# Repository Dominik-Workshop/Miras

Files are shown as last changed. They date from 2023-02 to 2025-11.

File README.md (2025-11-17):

# Miras

 


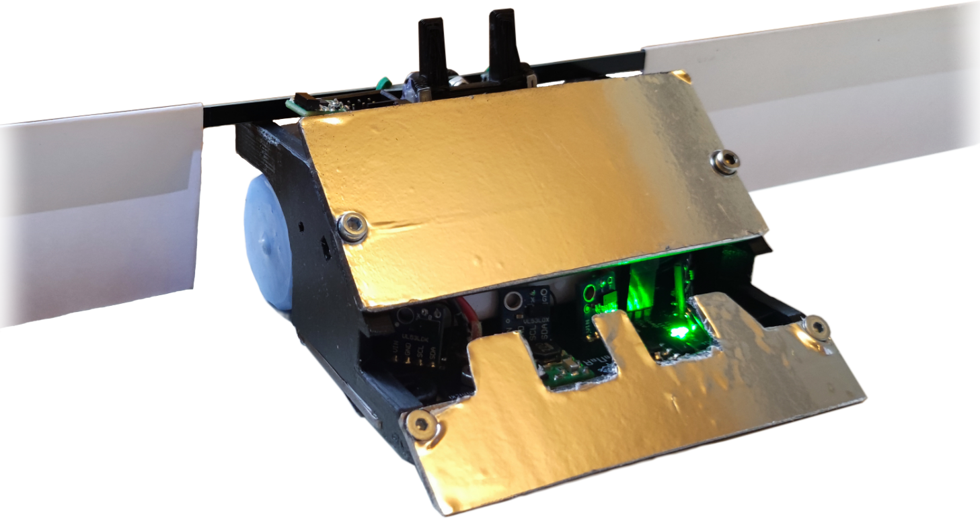
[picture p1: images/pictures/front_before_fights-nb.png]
Miras photo front


## Overview

Autonomous minisumo robot, based around an **STM32** microcontroller and **VL53L0X** TOF (time of flight) distance sensors, which provide necessary processing power and great detection range of opponents.

Its distinguishing feature is a set of **deployable wings**, designed to attract an opponent toward them, making them vulnerable to falling off the dohyo.

## Electronics

This project features two custom-designed PCBs that are connected via a flexible flat cable (FFC):

- [**Main board**](/pcb_main/): responsible for the robot's core functionalities. It integrates the microcontroller, sensors, motor drivers, and power management circuitry

<p align="center">
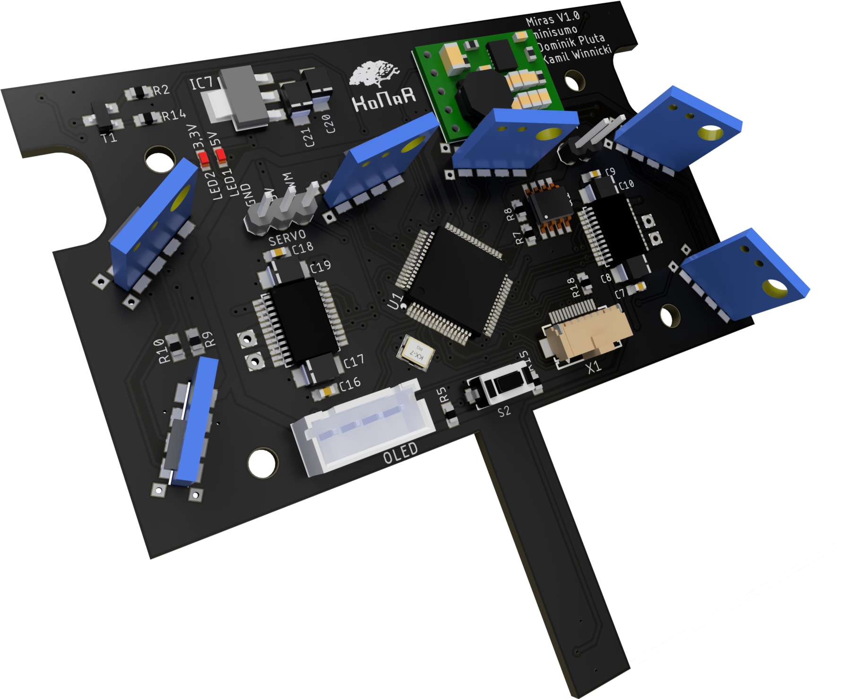
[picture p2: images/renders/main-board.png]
Main board render
  
</p>

- [**Top board**](/pcb_top/): accommodates an on/off switch, an SWD programming connector, configuration DIP switches, and a dedicated space for a standard [starter module](https://p1r.se/startmodule/)

<p align="center">
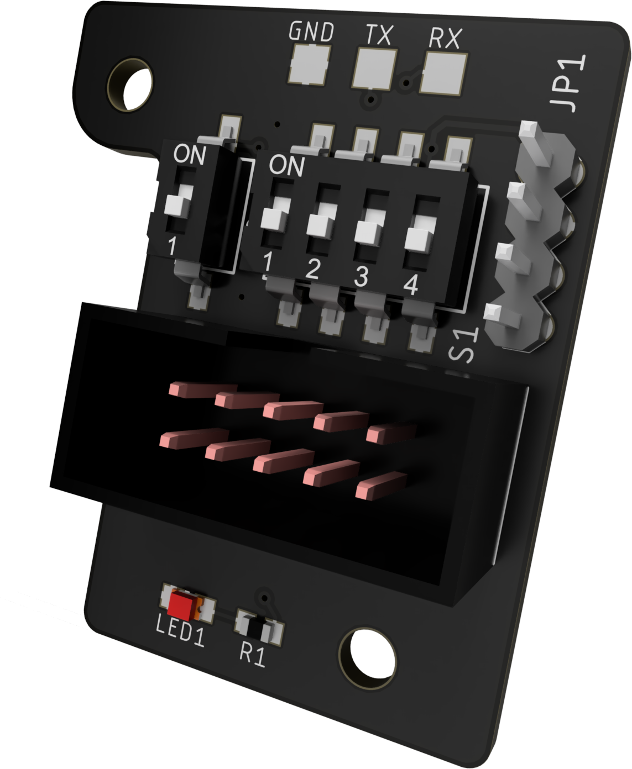
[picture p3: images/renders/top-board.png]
Top board render
   
</p>

The robot also features a 128x64px **OLED** screen for debugging.

<p align="center">
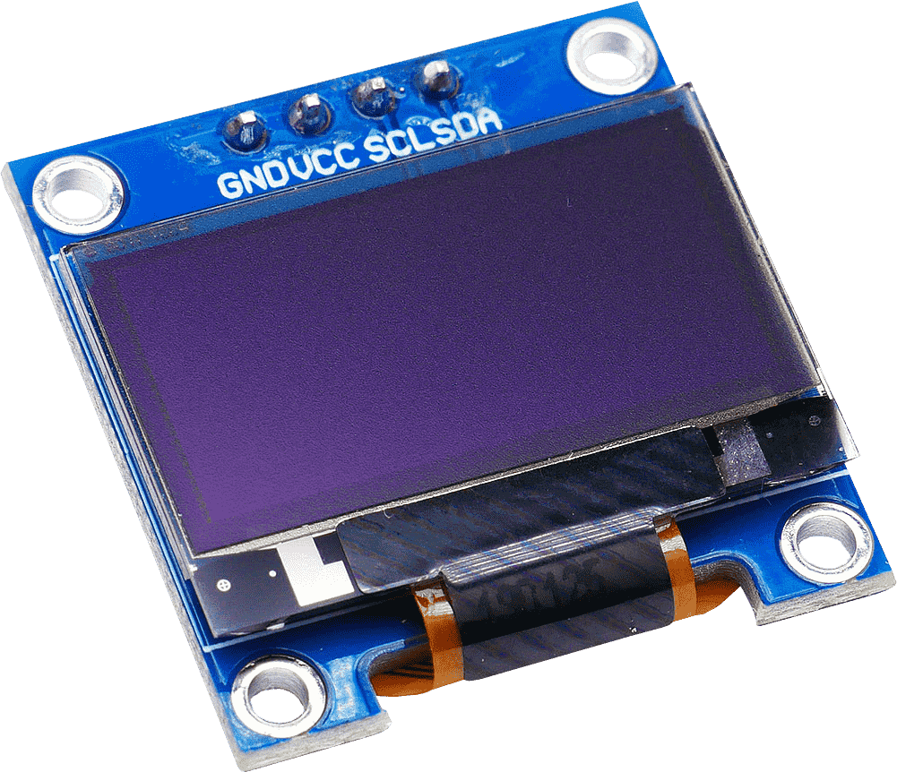
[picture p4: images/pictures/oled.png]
OLED photo
   
</p>

## Mechanical

<p align="center">
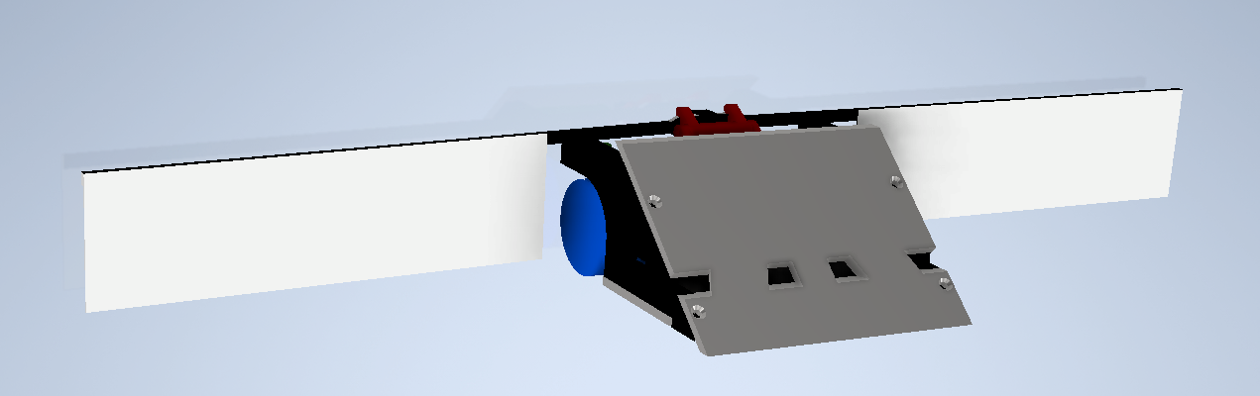
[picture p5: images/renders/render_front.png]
Miras render front
  
</p>

The chassis is a robust blend of 3D-printed components, steel, and aluminum, designed for durability and a low center of gravity. For superior traction on the dohyo, the robot is equipped with custom cast rubber tires. The unique deployable wings, made from lightweight paper, serve as the active deflection mechanism.

The robot is powered by two **N20** motors.

## Used Tools

- [Autodesk EAGLE](https://www.autodesk.com/products/eagle/) - Schematic and PCB design
- [Autodesk Inventor](https://www.autodesk.com/products/inventor/) - 3D modeling
- [STM32CubeIDE](https://www.st.com/en/development-tools/stm32cubeide.html) - STM32 firmware development (build/flash/debug)

## Authors

- [**Dominik Pluta**](https://github.com/Dominik-Workshop):
  - **Responsibility**: PCB design, programming
- [**Kamil Winnicki**](https://github.com/KamilWuu):
  - **Responsibility**: design and manufacturing of mechanical parts

## Special Thanks

Special thanks to [**Eryk Możdzeń**](https://github.com/Eryk-Mozdzen), who helped with programming.

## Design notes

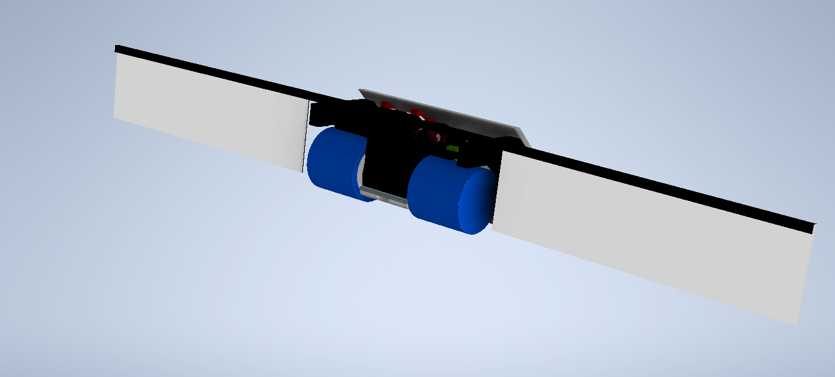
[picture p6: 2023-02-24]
images/renders/render_back.png

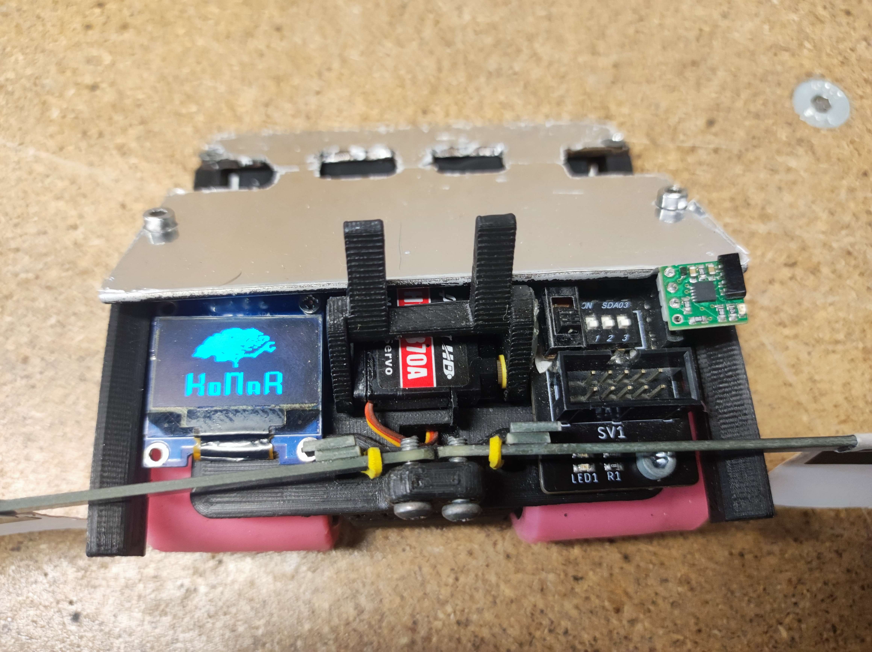
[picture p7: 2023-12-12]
images/pictures/top.jpg

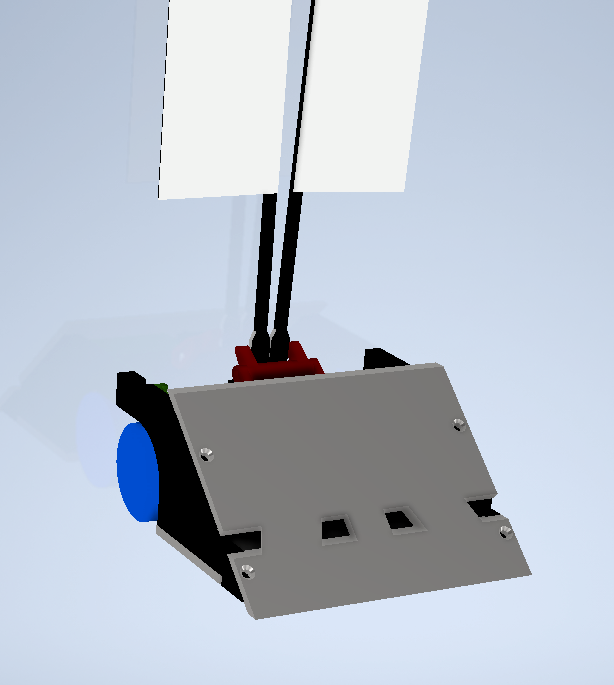
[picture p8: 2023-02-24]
images/renders/render_front_folded.png

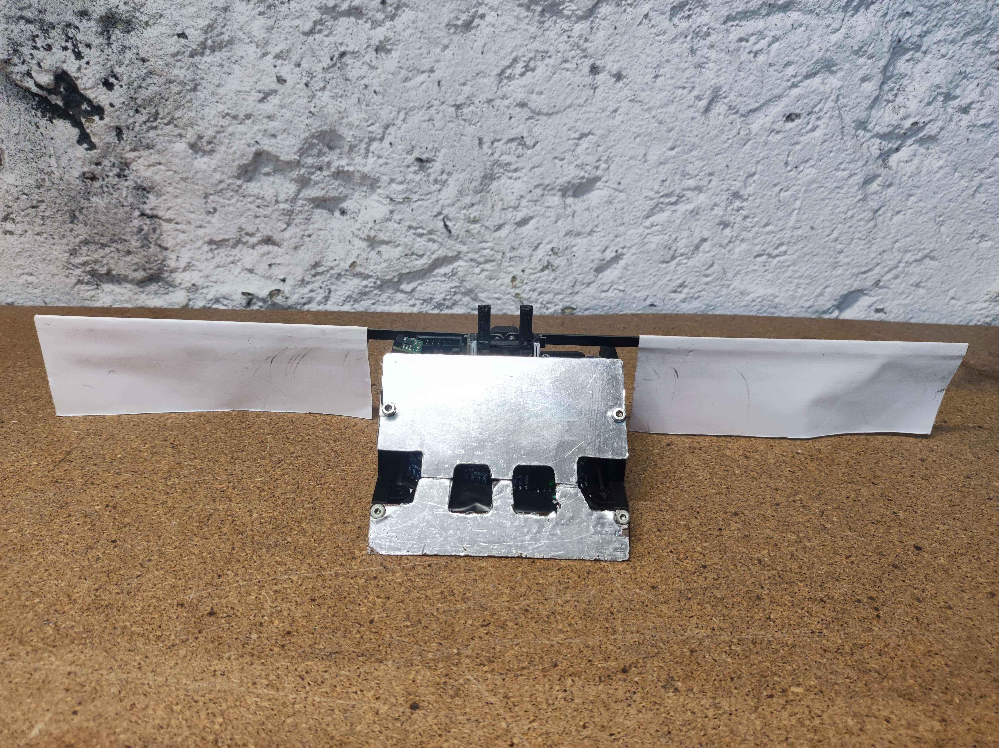
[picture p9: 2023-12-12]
images/pictures/front_down.jpg

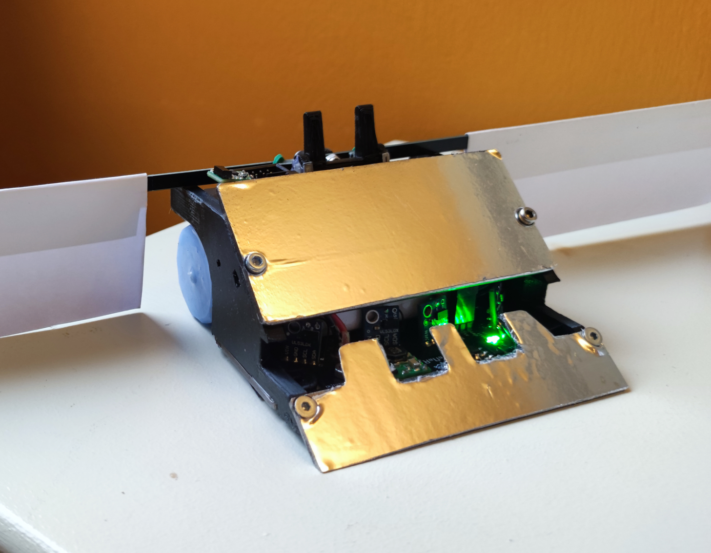
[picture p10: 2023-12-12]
images/pictures/front_before_fights.png

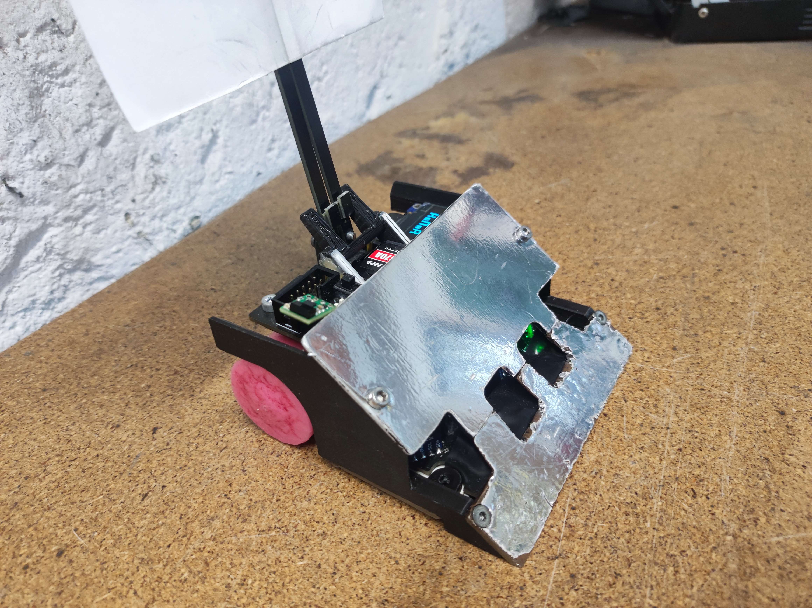
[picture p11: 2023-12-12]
images/pictures/front_angle_up.jpg

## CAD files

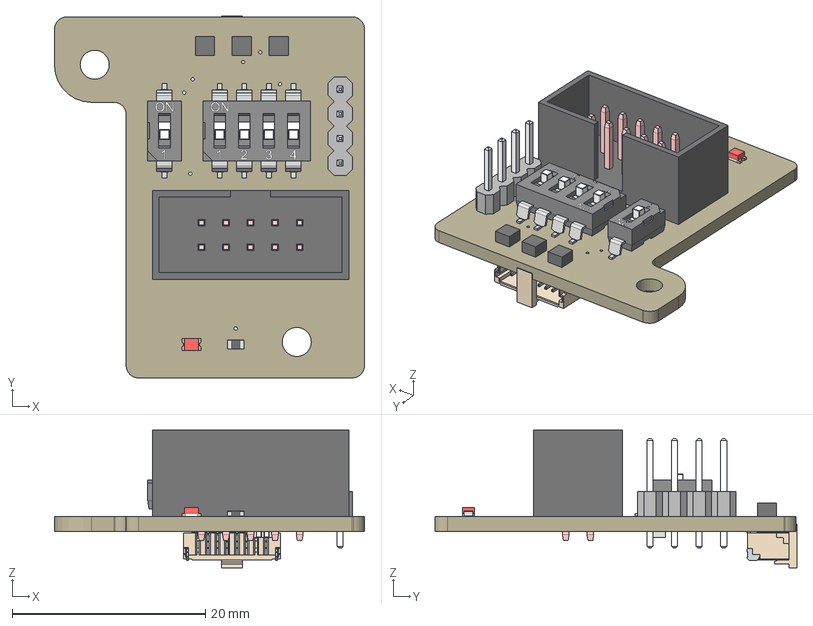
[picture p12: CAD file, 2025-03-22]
mechanics/pcb_top v5.step
32.0 x 37.4 x 14.2 mm
Board
ML10
6653xx124022_Pin x 7
6653xx124022_Solder_Tab x 2
6653xx124022_Cap
CAT16
SMS-001
SMS-004
1X04
CHIP-LED0805
R0603
TP20SQ x 3

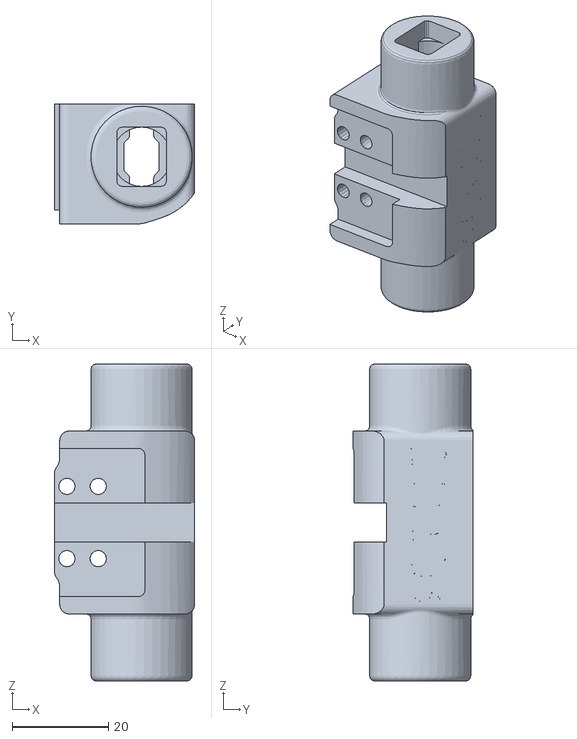
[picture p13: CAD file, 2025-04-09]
mechanics/stl/mototrs_Mount_miras_pololu_n20.stl
29.1 x 25.0 x 65.8

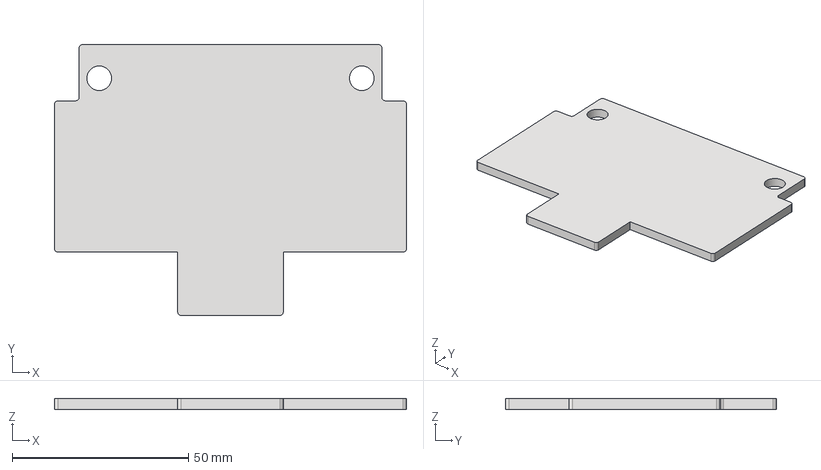
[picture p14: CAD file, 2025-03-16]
mechanics/plytka_stal_3mm.stp
100.0 x 77.0 x 3.00 mm

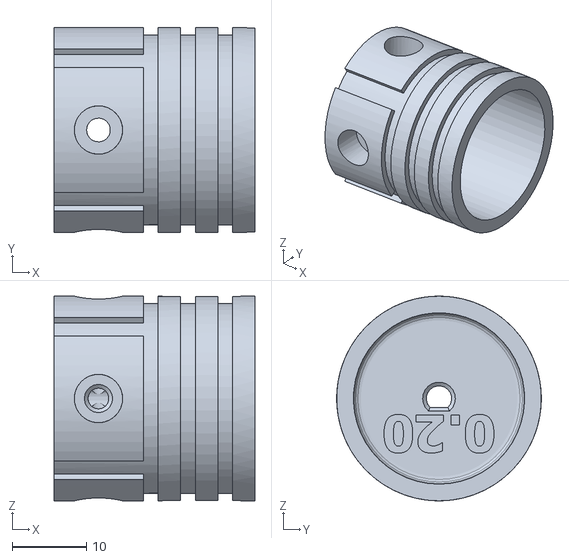
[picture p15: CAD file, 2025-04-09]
mechanics/stl/kolo_tetsowe_polololu_n20.stl
27.0 x 27.5 x 27.5

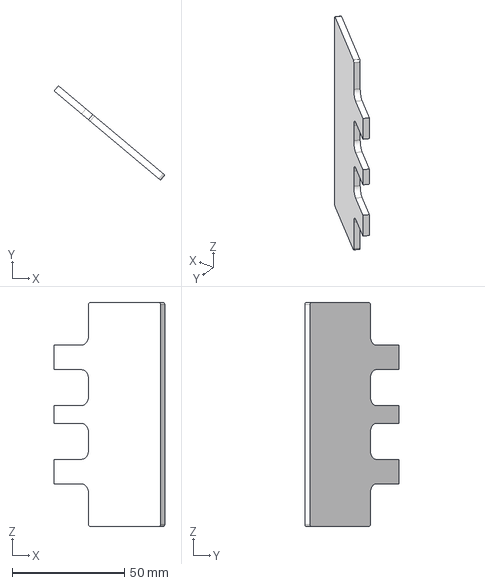
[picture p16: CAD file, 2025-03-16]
mechanics/pokrywa_stal_3mm.stp
49.4 x 42.2 x 100.0 mm

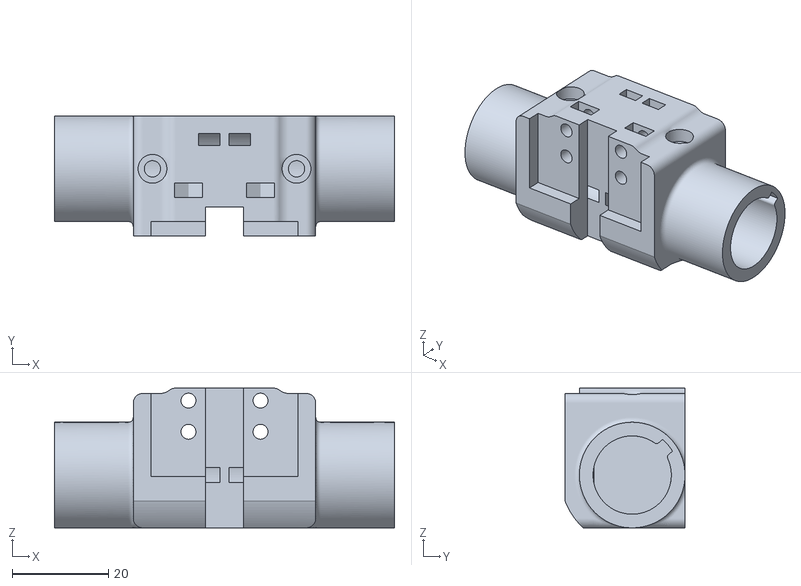
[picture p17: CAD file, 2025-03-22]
mechanics/stl/motors_mount_miras.stl
70.8 x 25.0 x 29.1

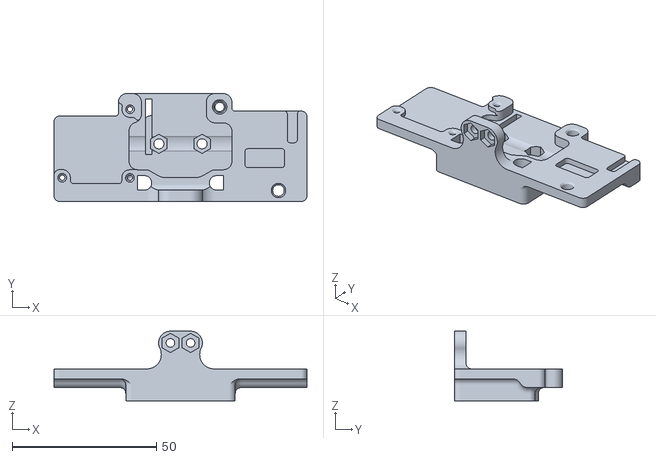
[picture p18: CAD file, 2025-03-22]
mechanics/stl/uchwyt na plytke.stl
87.8 x 37.5 x 24.2

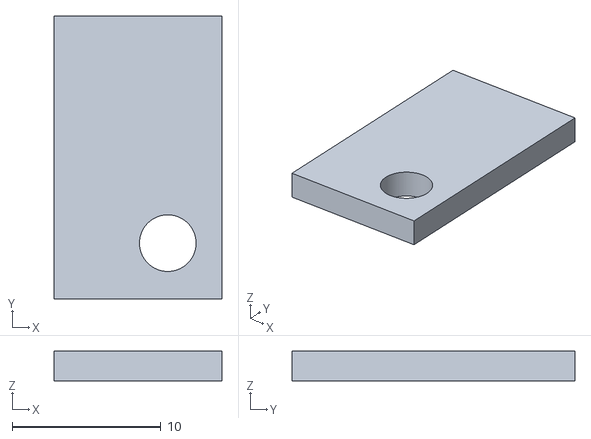
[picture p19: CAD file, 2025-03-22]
mechanics/stl/uchwyt_serwo.stl
11.2 x 19.0 x 2.00

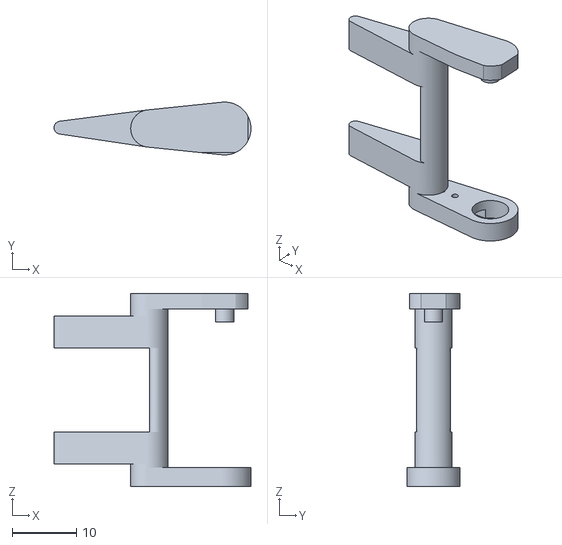
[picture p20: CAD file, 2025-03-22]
mechanics/stl/widelec.stl
30.6 x 8.20 x 30.0

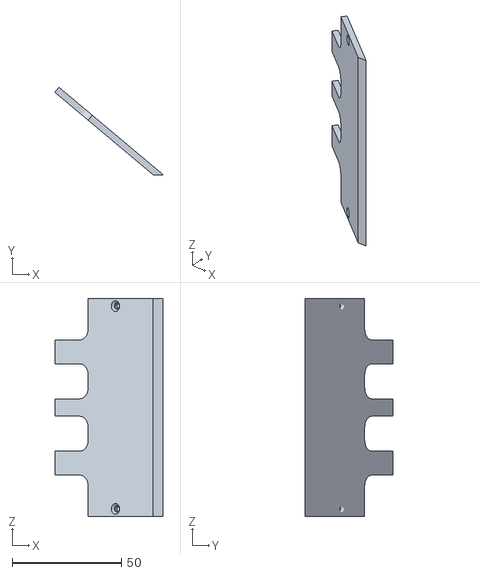
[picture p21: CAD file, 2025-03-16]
mechanics/stl/mirror.stl
49.8 x 40.1 x 100.0

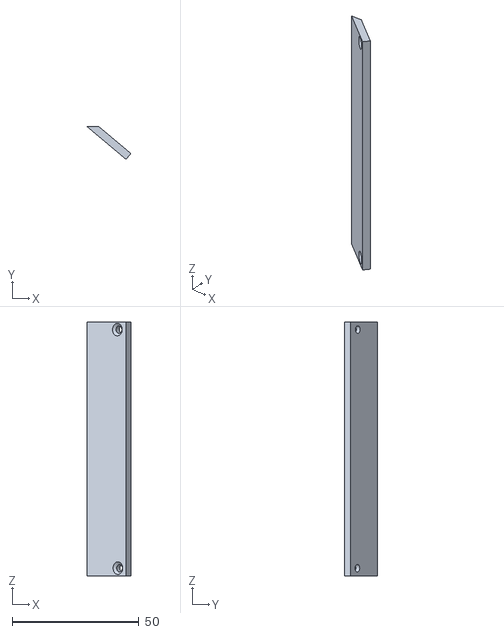
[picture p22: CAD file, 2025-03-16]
mechanics/stl/strug.stl
17.2 x 12.9 x 100.0

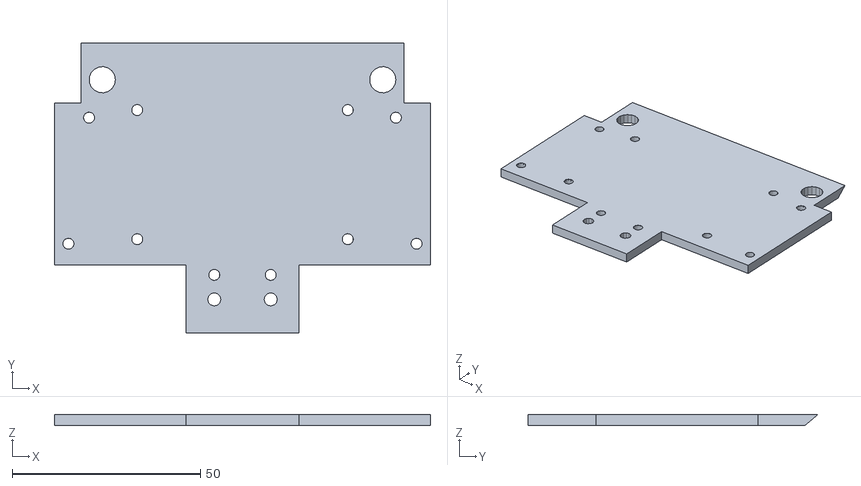
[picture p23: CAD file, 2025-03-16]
mechanics/stl/blacha_stal_3mm.stl
100.0 x 77.2 x 3.00

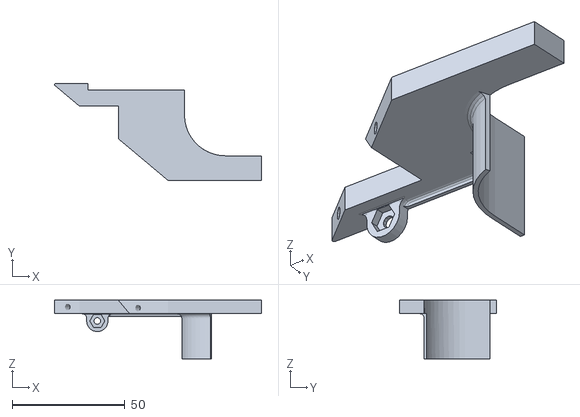
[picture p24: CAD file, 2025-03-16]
mechanics/stl/sciana.stl
91.9 x 43.1 x 26.0

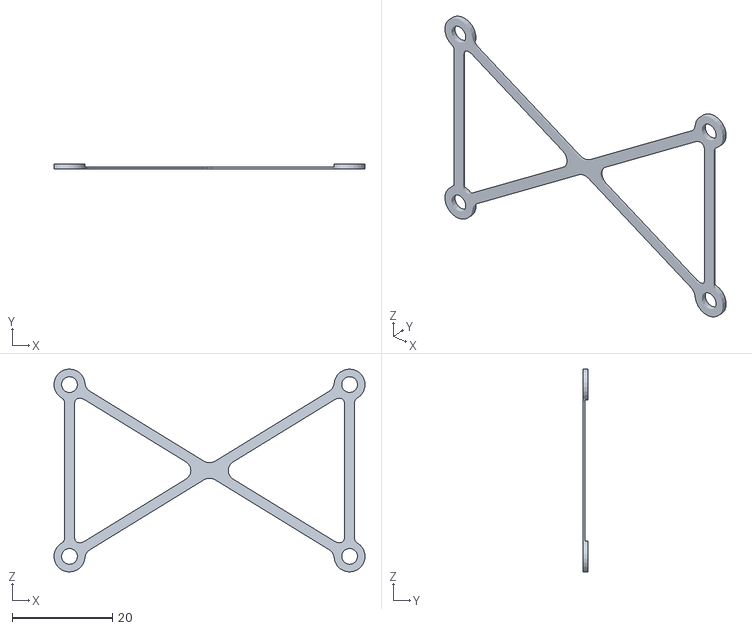
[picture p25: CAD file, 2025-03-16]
mechanics/stl/pcb_podstawka.stl
62.2 x 1.00 x 40.5

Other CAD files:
mechanics/stl/motors_mount_miras_v2.stl
mechanics/stl/kolo_tetsowe.stl
mechanics/Minisumokokszloz.iam
mechanics/Miras.iam
mechanics/OldVersions/Minisumokokszloz.0003.iam
mechanics/OldVersions/Miras.0025.iam
mechanics/OldVersions/PCB.0011.ipt
mechanics/OldVersions/PCB_2_Miras.0002.ipt
mechanics/OldVersions/Part12.0001.ipt
mechanics/OldVersions/Part6.0001.ipt
mechanics/OldVersions/Part8.0006.ipt
mechanics/OldVersions/Part9.0001.ipt
mechanics/OldVersions/Serwo_z_widelcem.0002.iam
mechanics/OldVersions/TOF_VLCOS.0002.ipt
mechanics/OldVersions/blacha_stal_3mm.0005.ipt
mechanics/OldVersions/dół.0002.ipt
mechanics/OldVersions/felga.0005.ipt
mechanics/OldVersions/koks.0001.iam
mechanics/OldVersions/koks_v3.0007.iam
mechanics/OldVersions/kolo_tetsowe.0007.ipt
mechanics/OldVersions/kąty.0003.iam
mechanics/OldVersions/lead.0001.ipt
mechanics/OldVersions/lead_3.0005.ipt
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

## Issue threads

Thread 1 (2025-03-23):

Design a flex PCB for distance sensors

Dominik-Workshop, 2025-03-23:
Currently, ready-made modules containing VL53L0X TOF distance sensors are used. However, due to their physical design, these sensors must be positioned relatively far from the robot's outer walls. This requires large cutouts in the walls to ensure the sensors don't detect the walls themselves.

To address this, a custom flexible PCB should be designed to accommodate the TOF distance sensors. This will allow the sensors to be placed closer to the robot's outer walls, minimizing the size of the required cutouts. Additionally, a mechanical structure should be designed to securely mount the sensors in their optimal positions.

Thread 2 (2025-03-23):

Design a mount for the flexible PCB with distance sensors

Dominik-Workshop, 2025-03-23:
Design a mechanical structure to securely mount a custom flexible PCB with VL53L0X TOF, which is designed in #1.

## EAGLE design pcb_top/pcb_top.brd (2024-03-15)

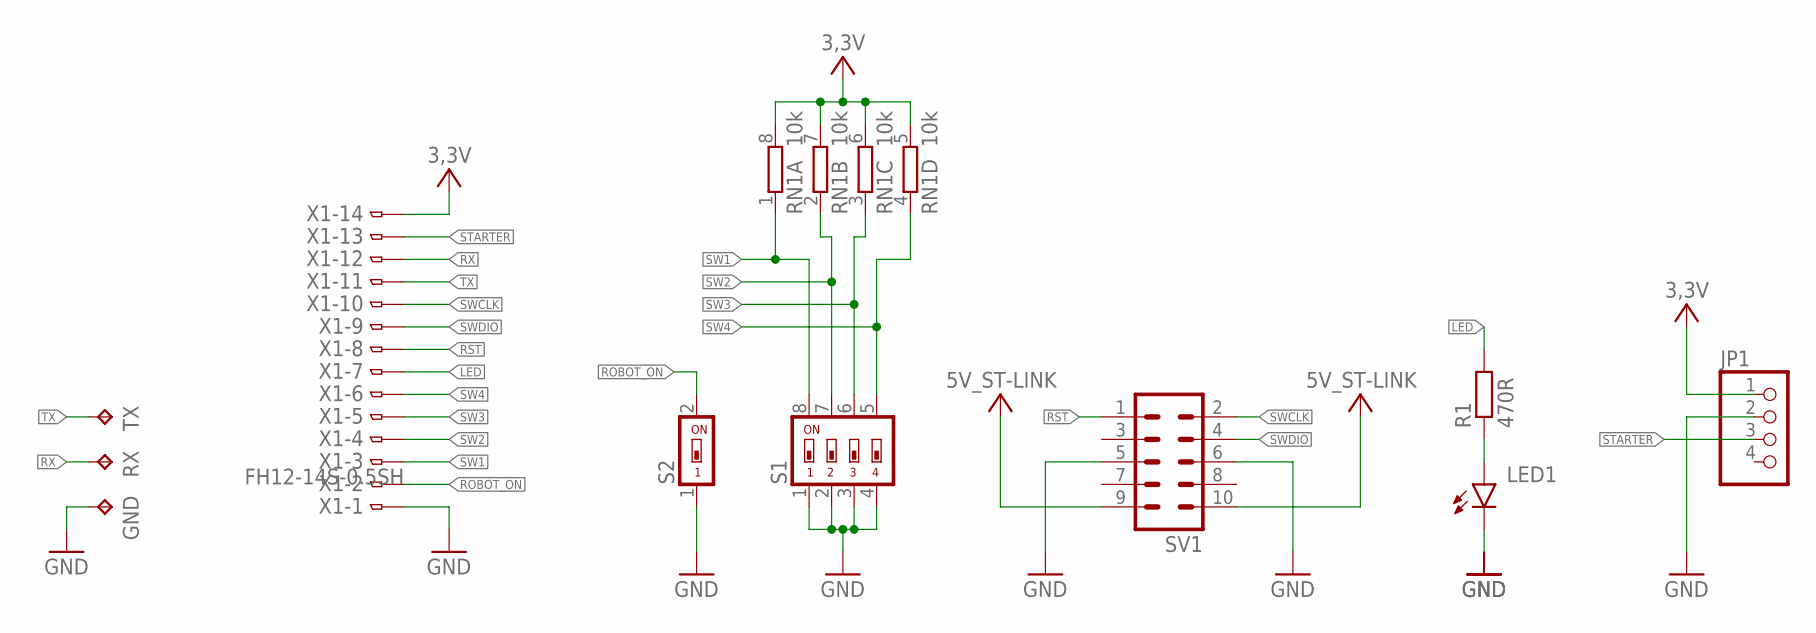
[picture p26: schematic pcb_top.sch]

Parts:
GND: TPTP20SQ; TP20SQ
JP1: PINHD-1X4; 1X04
LED1: LEDCHIP-LED0805; CHIP-LED0805
R1: 470R; R0603
RN1: 10k; CAT16
RX: TPTP20SQ; TP20SQ
S1: SWS004; SMS-004
S2: SWS001; SMS-001
SV1: ML10
TX: TPTP20SQ; TP20SQ
X1: FH12-14S-0.5SH

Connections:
3,3V: JP1.1, RN1.5 (2), RN1.6 (2), RN1.7 (2), RN1.8 (2), X1.14
5V_ST-LINK: SV1.9, SV1.10
GND: GND.TP, JP1.2, LED1.C, S1.1, S1.2, S1.3, S1.4, S2.1, SV1.5, SV1.6, X1.1
LED: R1.2, X1.7
unnamed: LED1.A, R1.1
ROBOT_ON: S2.2, X1.2
RST: SV1.1, X1.8
RX: RX.TP, X1.12
STARTER: JP1.3, X1.13
SW1: RN1.1, S1.8, X1.3
SW2: RN1.2 (1), S1.7, X1.4
SW3: RN1.3 (1), S1.6, X1.5
SW4: RN1.4 (1), S1.5, X1.6
SWCLK: SV1.2, X1.10
SWDIO: SV1.4, X1.9
TX: TX.TP, X1.11

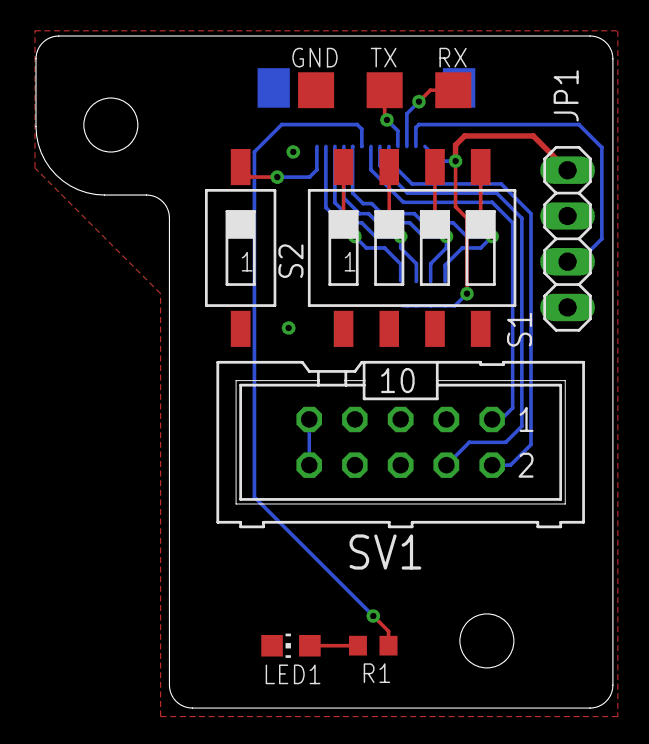
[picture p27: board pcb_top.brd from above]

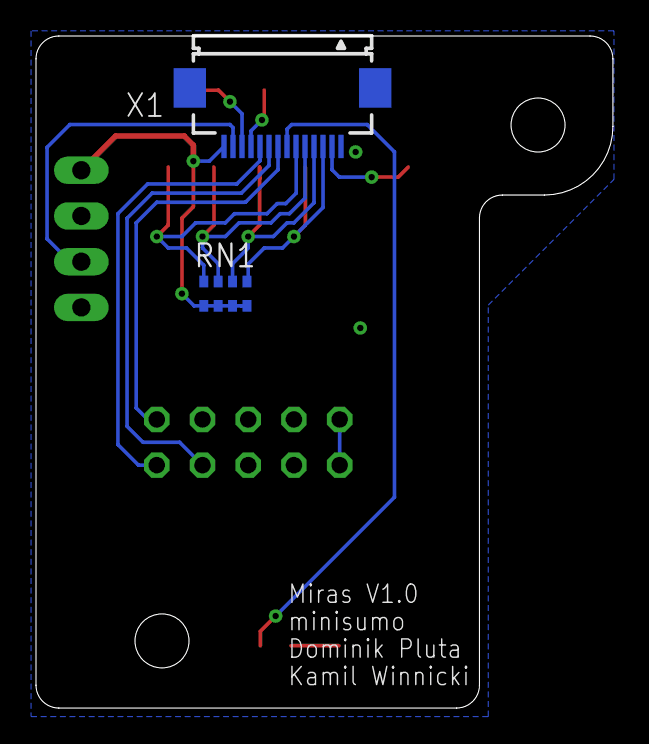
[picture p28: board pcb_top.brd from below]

Board: 2 copper layers, 32.0 x 37.3 mm, 11 parts (2 on the bottom side), 16 nets.

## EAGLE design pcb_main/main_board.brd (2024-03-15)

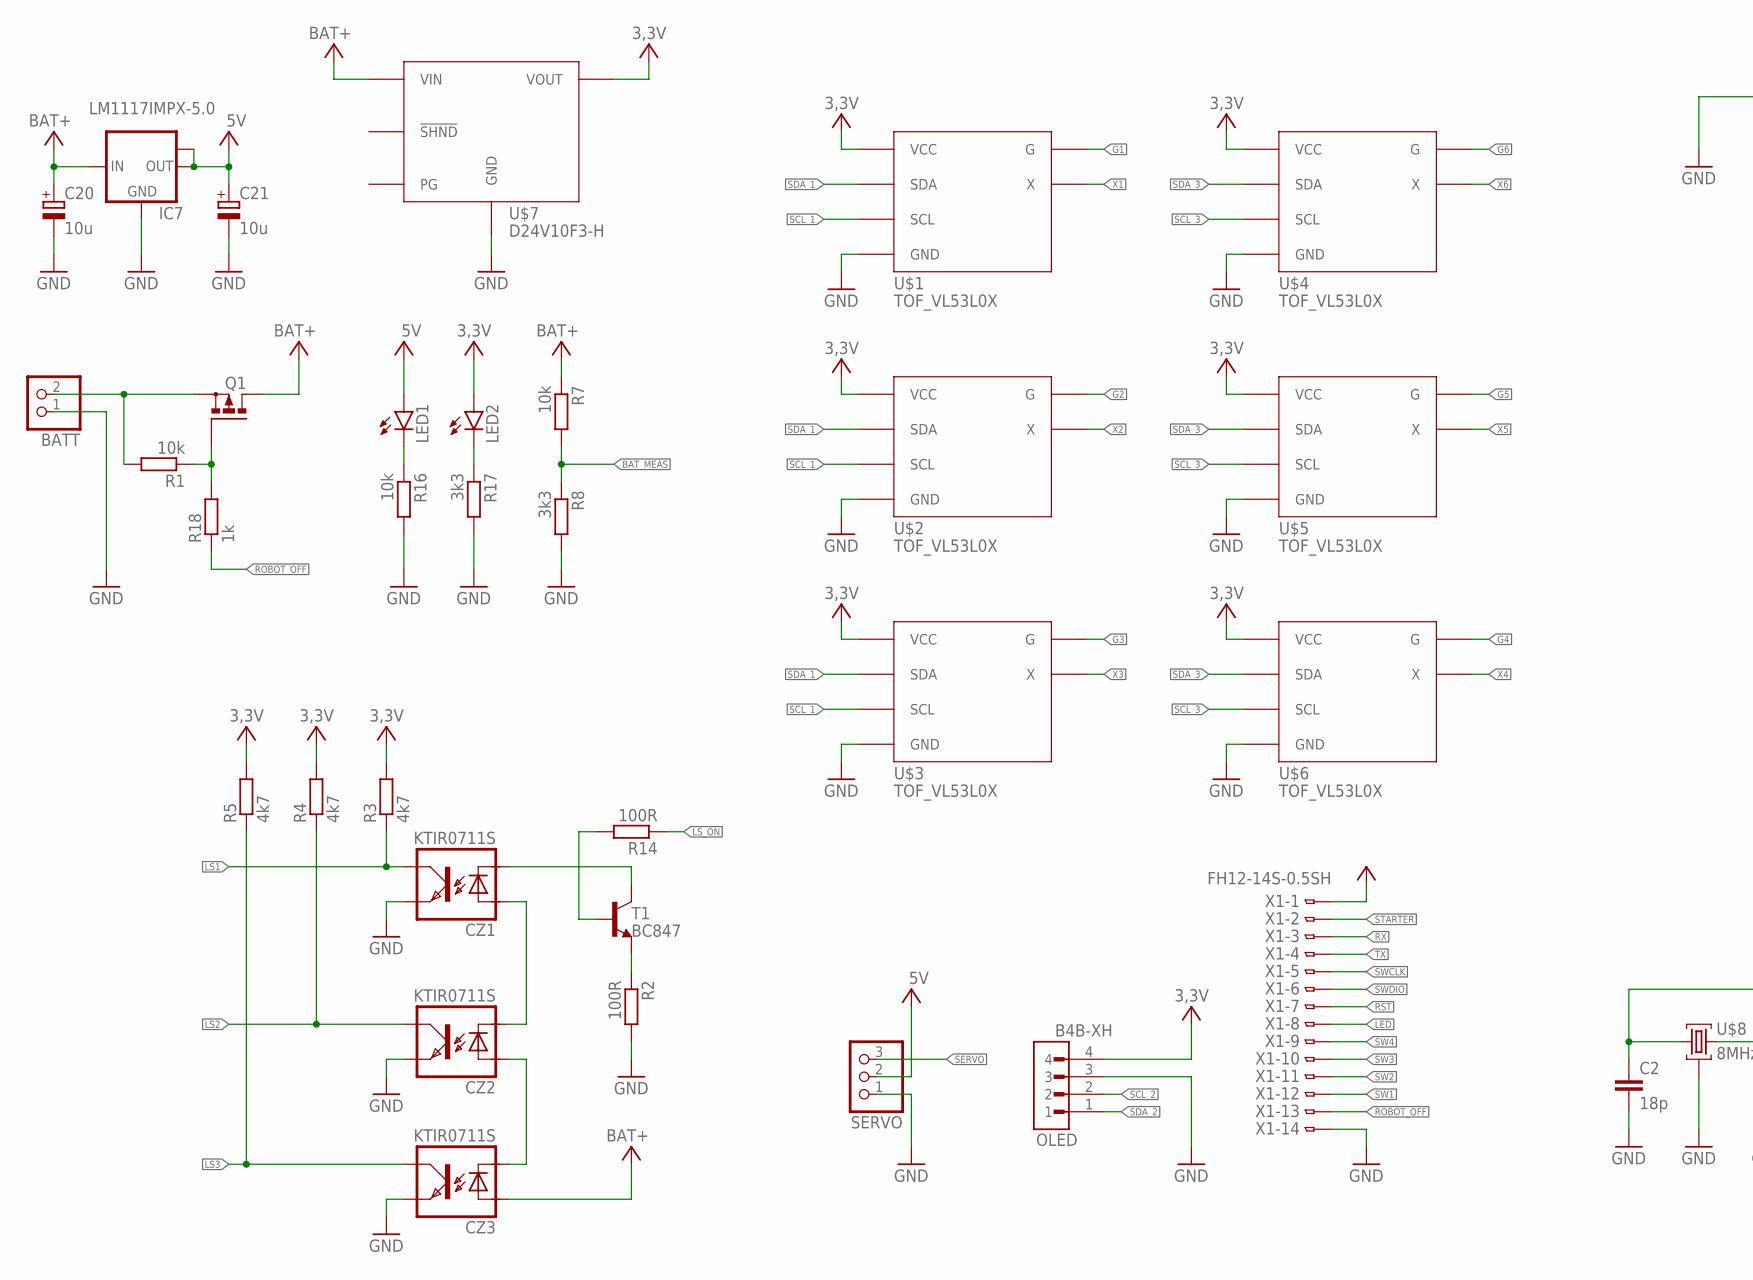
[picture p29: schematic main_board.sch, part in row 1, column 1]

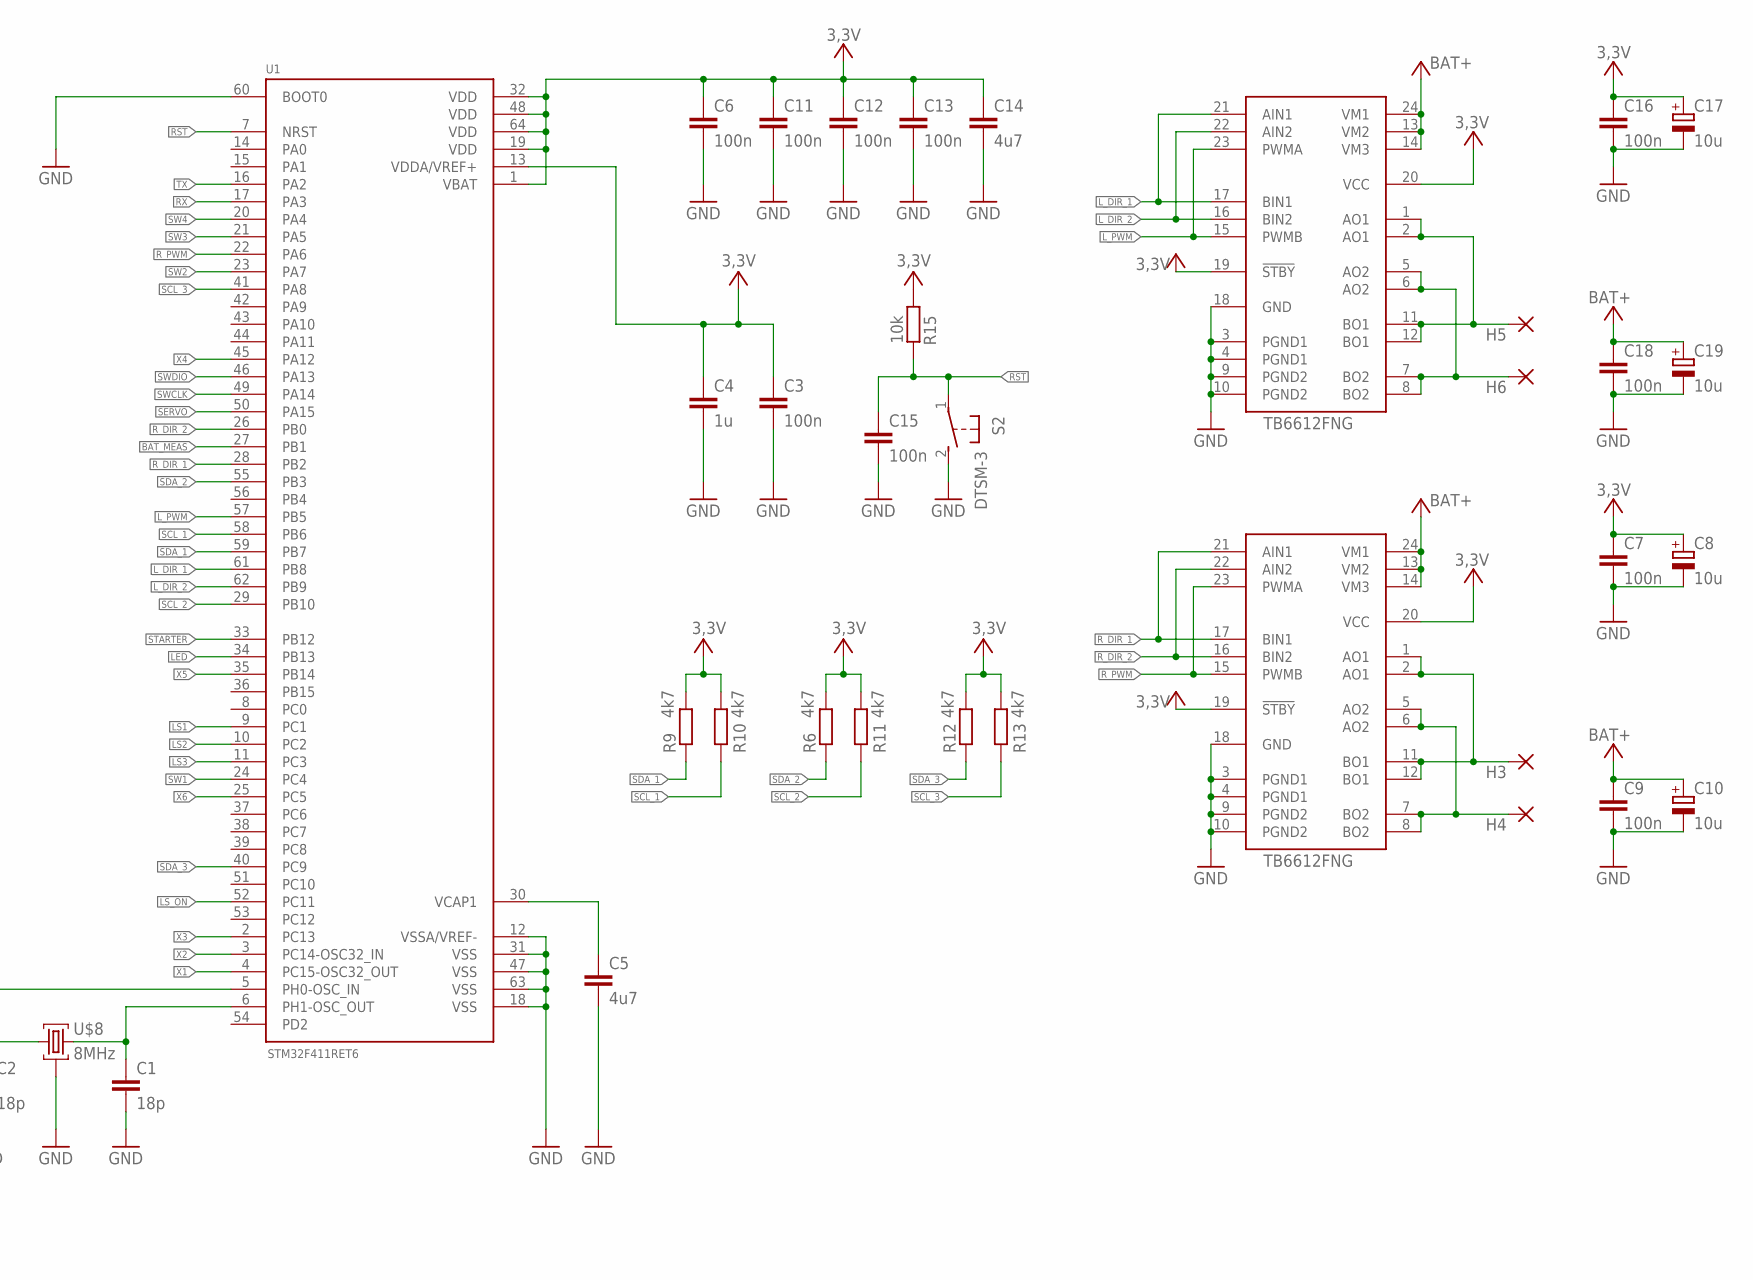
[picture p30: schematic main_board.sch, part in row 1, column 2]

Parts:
BATT: PINHD-1X2; 1X02
C1, C2: 18p; C0603
C3, C6, C7, C9, C11, C12, C13, C15, C16, C18: 100n; C0603
C4: 1u; C0603
C5, C14: 4u7; C0603
C8, C10, C17, C19, C20, C21: 10u; B/3528-21W
CZ1, CZ2, CZ3: KTIR0711S; TOP
H3, H4, H5, H6: 1,6/0,8
IC7: LM1117IMPX-5.0; SOT223
LED1, LED2: LEDCHIPLED_0603; CHIPLED_0603
OLED: B4B-XH; JST_B4B-XH-A(LF)(SN)
Q1: P-MOSFET-SO8; SO-08
R1, R7, R15, R16: 10k; R0603
R2, R14: 100R; R0603
R3, R4, R5, R6, R9, R10, R11, R12, R13: 4k7; R0603
R8, R17: 3k3; R0603
R18: 1k; R0603
S2: DTSM-3
SERVO: PINHD-1X3; 1X03
T1: BC847; SOT23
TB6612, TB6612_: TB6612FNG; SSOP24
U1: STM32F411RET6; QFP50P1200X1200X160-64N
U$1, U$2, U$3, U$4, U$5, U$6: TOF_VL53L0X
U$7: D24V10F3-H
U$8: 8MHz; CRYSTAL_3,4X2,7
X1: FH12-14S-0.5SH

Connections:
3,3V: C3.1, C4.1, C6.1, C7.1, C8.+, C11.1, C12.1, C13.1, C14.1, C16.1, C17.+, LED2.A, OLED.4, R3.2, R4.2, R5.2, R6.2, R9.2, R10.2, R11.2, R12.2, R13.2, R15.1, TB6612.19 (!STBY), TB6612.20 (VCC), TB6612_.19 (!STBY), TB6612_.20 (VCC), U1.1 (VBAT), U1.13 (VDDA/VREF+), U1.19 (VDD), U1.32 (VDD), U1.48 (VDD), U1.64 (VDD), U$1.VCC, U$1.VCC_ (VCC), U$2.VCC, U$2.VCC_ (VCC), U$3.VCC, U$3.VCC_ (VCC), U$4.VCC, U$4.VCC_ (VCC), U$5.VCC, U$5.VCC_ (VCC), U$6.VCC, U$6.VCC_ (VCC), U$7.VOUT, X1.1
5V: C21.+, IC7.2 (OUT), IC7.TAB (OUT1), LED1.A, SERVO.2
BAT: BATT.2, Q1.1 (S), Q1.2 (S), Q1.3 (S), R1.2
BAT+: C9.1, C10.+, C18.1, C19.+, C20.+, CZ3.ANODA, IC7.3 (IN), Q1.5 (D), Q1.6 (D), Q1.7 (D), Q1.8 (D), R7.1, TB6612.13 (VM2), TB6612.14 (VM3), TB6612.24 (VM1), TB6612_.13 (VM2), TB6612_.14 (VM3), TB6612_.24 (VM1), U$7.VIN
BAT_MEAS: R7.2, R8.1, U1.27 (PB1)
BO1: H3.1, TB6612.1 (AO1), TB6612.2 (AO1), TB6612.11 (BO1), TB6612.12 (BO1)
BO2: H4.1, TB6612.5 (AO2), TB6612.6 (AO2), TB6612.7 (BO2), TB6612.8 (BO2)
BO3: H5.1, TB6612_.1 (AO1), TB6612_.2 (AO1), TB6612_.11 (BO1), TB6612_.12 (BO1)
BO4: H6.1, TB6612_.5 (AO2), TB6612_.6 (AO2), TB6612_.7 (BO2), TB6612_.8 (BO2)
G1: U$1.G
G2: U$2.G
G3: U$3.G
G4: U$6.G
G5: U$5.G
G6: U$4.G
GND: BATT.1, C1.2, C2.2, C3.2, C4.2, C5.2, C6.2, C7.2, C8.-, C9.2, C10.-, C11.2, C12.2, C13.2, C14.2, C15.2, C16.2, C17.-, C18.2, C19.-, C20.-, C21.-, CZ1.EMITER, CZ2.EMITER, CZ3.EMITER, IC7.1 (GND), OLED.3, R2.2, R8.2, R16.2, R17.2, S2.2, SERVO.1, TB6612.3 (PGND1), TB6612.4 (PGND1), TB6612.9 (PGND2), TB6612.10 (PGND2), TB6612.18 (GND), TB6612_.3 (PGND1), TB6612_.4 (PGND1), TB6612_.9 (PGND2), TB6612_.10 (PGND2), TB6612_.18 (GND), U1.12 (VSSA/VREF-), U1.18 (VSS), U1.31 (VSS), U1.47 (VSS), U1.60 (BOOT0), U1.63 (VSS), U$1.GND, U$1.GND_ (GND), U$2.GND, U$2.GND_ (GND), U$3.GND, U$3.GND_ (GND), U$4.GND, U$4.GND_ (GND), U$5.GND, U$5.GND_ (GND), U$6.GND, U$6.GND_ (GND), U$7.GND, U$8.GND (2), U$8.GND2 (2), X1.14
LED: U1.34 (PB13), X1.8
LS1: CZ1.KOLEKTOR, R3.1, U1.9 (PC1)
LS2: CZ2.KOLEKTOR, R4.1, U1.10 (PC2)
LS3: CZ3.KOLEKTOR, R5.1, U1.11 (PC3)
LS_ON: R14.1, U1.52 (PC11)
L_DIR_1: TB6612_.17 (BIN1), TB6612_.21 (AIN1), U1.61 (PB8)
L_DIR_2: TB6612_.16 (BIN2), TB6612_.22 (AIN2), U1.62 (PB9)
L_PWM: TB6612_.15 (PWMB), TB6612_.23 (PWMA), U1.57 (PB5)
unnamed: LED1.C, R16.1
unnamed: CZ1.KATODA, T1.3 (C)
unnamed: CZ1.ANODA, CZ2.KATODA
unnamed: CZ2.ANODA, CZ3.KATODA
unnamed: R14.2, T1.1 (B)
unnamed: R2.1, T1.2 (E)
unnamed: LED2.C, R17.1
unnamed: Q1.4 (G), R1.1, R18.2
ROBOT_OFF: R18.1, X1.13
RST: C15.1, R15.2, S2.1, U1.7 (NRST), X1.7
RX: U1.17 (PA3), X1.3
R_DIR_1: TB6612.17 (BIN1), TB6612.21 (AIN1), U1.28 (PB2)
R_DIR_2: TB6612.16 (BIN2), TB6612.22 (AIN2), U1.26 (PB0)
R_PWM: TB6612.15 (PWMB), TB6612.23 (PWMA), U1.22 (PA6)
SCL_1: R10.1, U1.58 (PB6), U$1.SCL, U$1.SCL_ (SCL), U$2.SCL, U$2.SCL_ (SCL), U$3.SCL, U$3.SCL_ (SCL)
SCL_2: OLED.2, R11.1, U1.29 (PB10)
SCL_3: R13.1, U1.41 (PA8), U$4.SCL, U$4.SCL_ (SCL), U$5.SCL, U$5.SCL_ (SCL), U$6.SCL, U$6.SCL_ (SCL)
SDA_1: R9.1, U1.59 (PB7), U$1.SDA, U$1.SDA_ (SDA), U$2.SDA, U$2.SDA_ (SDA), U$3.SDA, U$3.SDA_ (SDA)
SDA_2: OLED.1, R6.1, U1.55 (PB3)
SDA_3: R12.1, U1.40 (PC9), U$4.SDA, U$4.SDA_ (SDA), U$5.SDA, U$5.SDA_ (SDA), U$6.SDA, U$6.SDA_ (SDA)
SERVO: SERVO.3, U1.50 (PA15)
STARTER: U1.33 (PB12), X1.2
SW1: U1.24 (PC4), X1.12
SW2: U1.23 (PA7), X1.11
SW3: U1.21 (PA5), X1.10
SW4: U1.20 (PA4), X1.9
SWCLK: U1.49 (PA14), X1.5
SWDIO: U1.46 (PA13), X1.6
TX: U1.16 (PA2), X1.4
VCAP: C5.1, U1.30 (VCAP1)
X1: U1.4 (PC15-OSC32_OUT), U$1.X
X2: U1.3 (PC14-OSC32_IN), U$2.X
X3: U1.2 (PC13), U$3.X
X4: U1.45 (PA12), U$6.X
X5: U1.35 (PB14), U$5.X
X6: U1.25 (PC5), U$4.X
XTAL1: C2.1, U1.5 (PH0-OSC_IN), U$8.CRST1 (1)
XTAL2: C1.1, U1.6 (PH1-OSC_OUT), U$8.CRST2 (3)

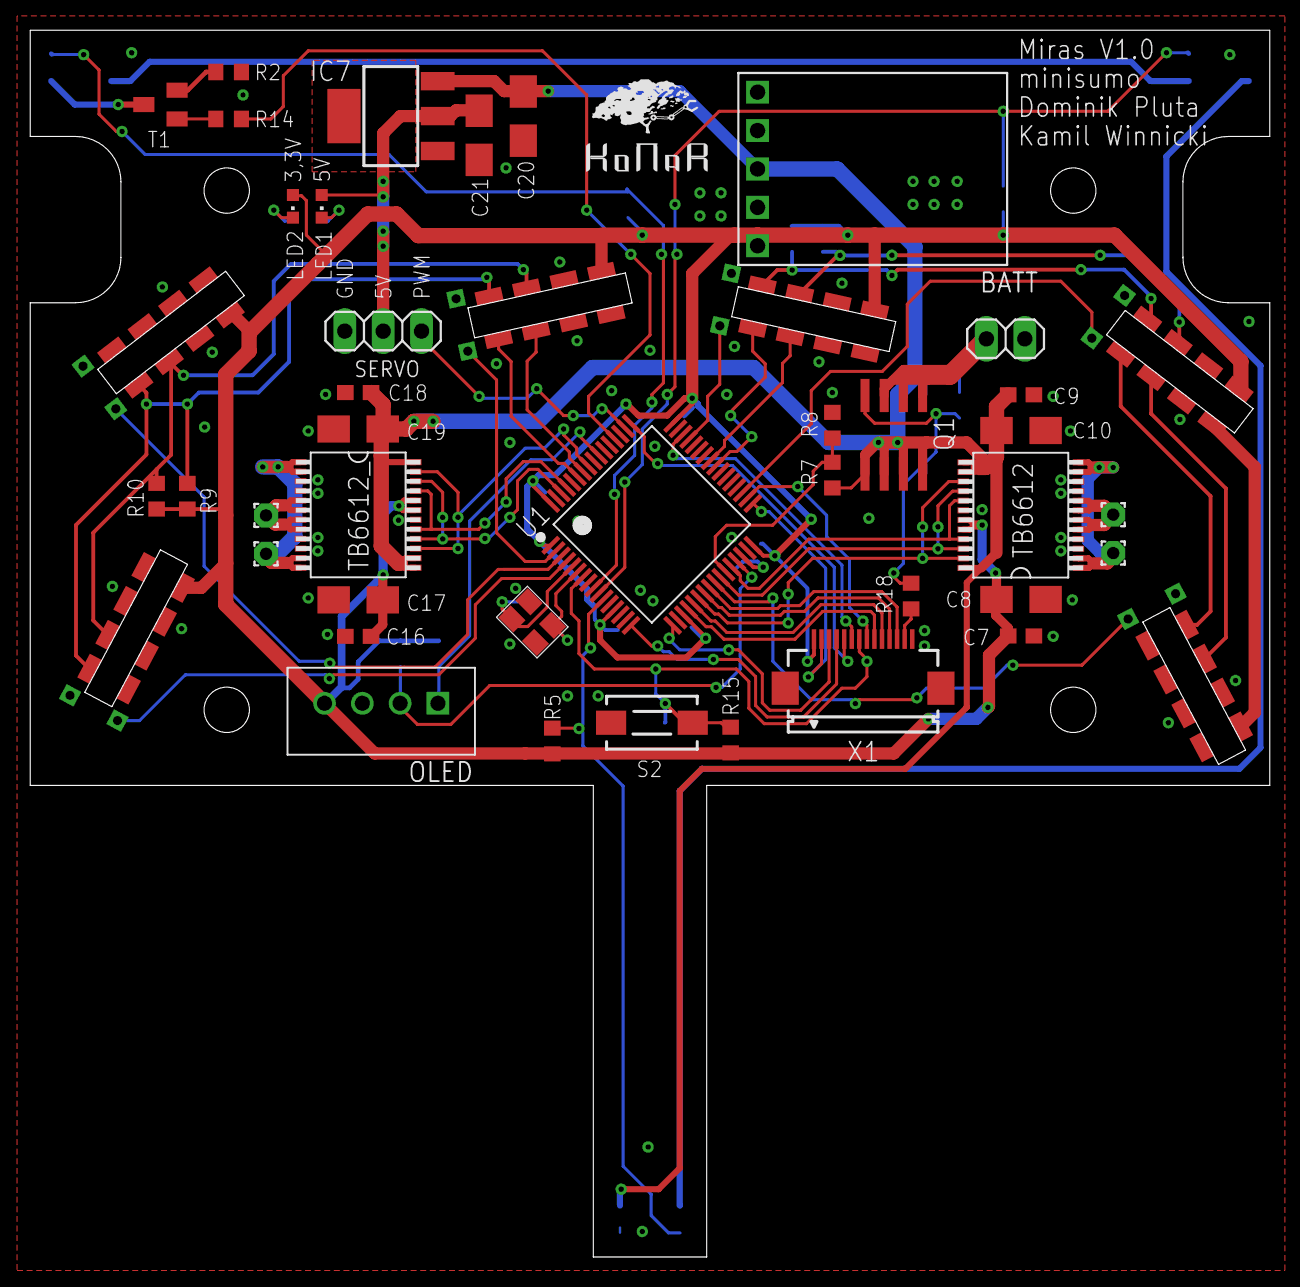
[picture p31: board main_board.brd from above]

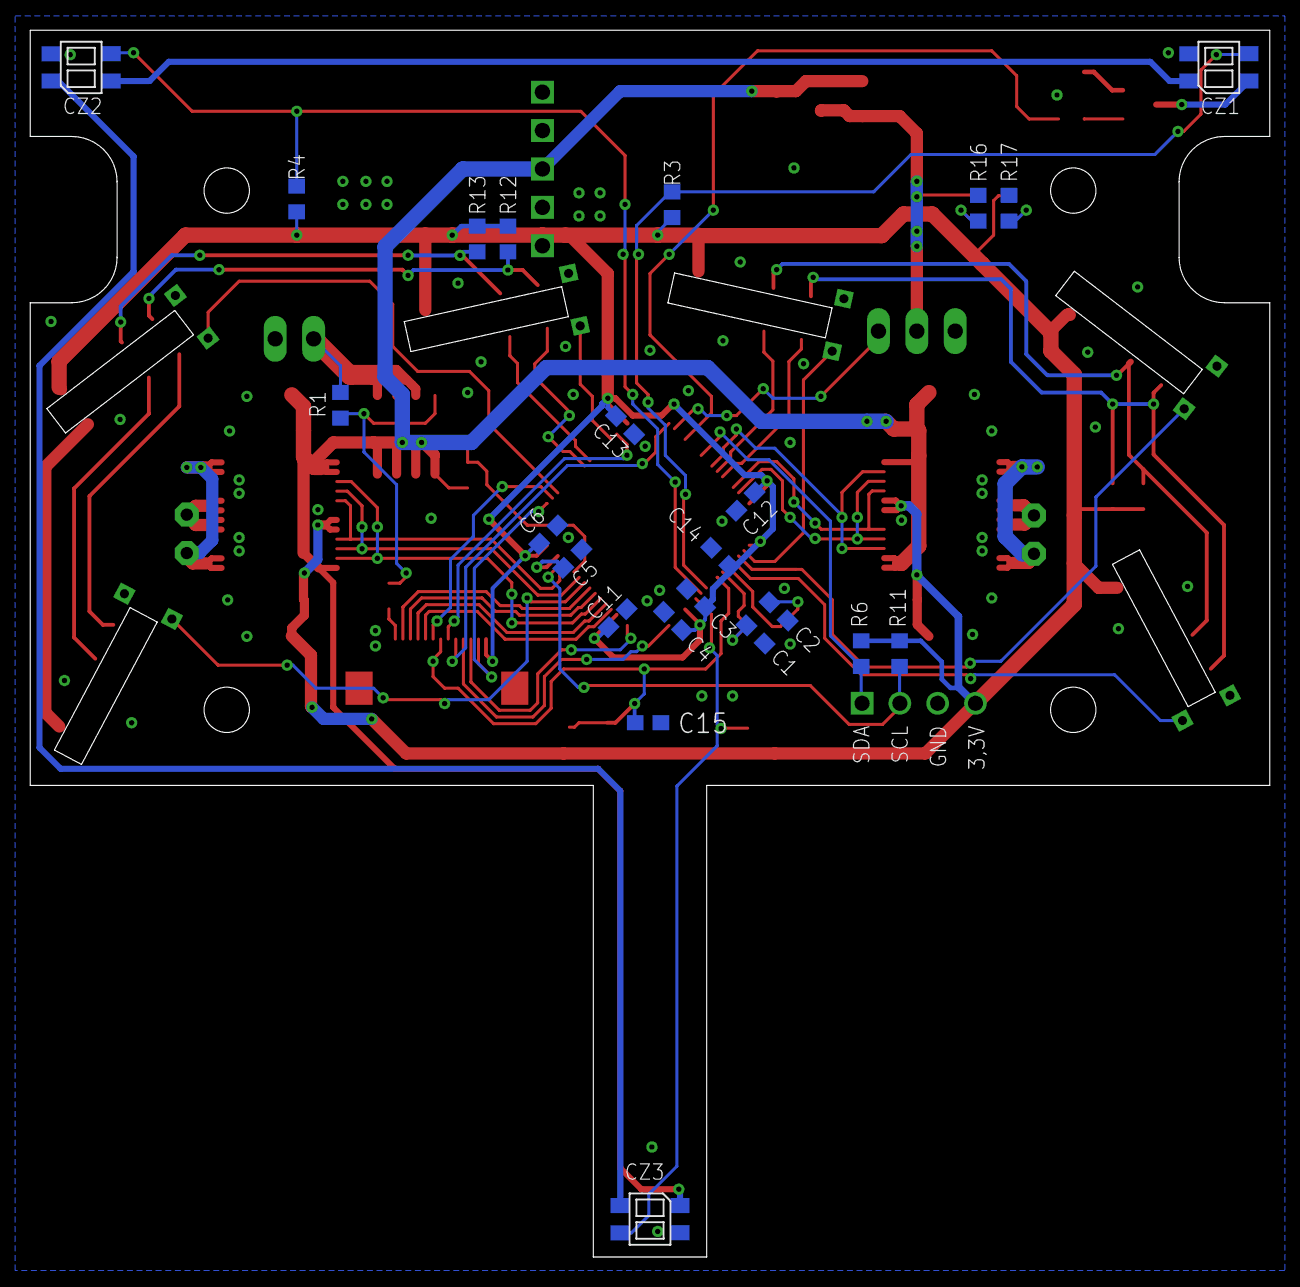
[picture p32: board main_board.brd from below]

Board: 2 copper layers, 82.0 x 81.2 mm, 67 parts (23 on the bottom side), 56 nets.

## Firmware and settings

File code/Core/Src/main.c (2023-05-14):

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
/* Includes ------------------------------------------------------------------*/
#include "main.h"

/* USER CODE BEGIN Includes */
#include "modes_of_operation.h"
#include "display.h"
#include "battery.h"
#include "motors.h"
#include "vl53l0x_api.h"
#include "vl53l0_init.h"
/* USER CODE END Includes */

ADC_HandleTypeDef hadc1;
DMA_HandleTypeDef hdma_adc1;

I2C_HandleTypeDef hi2c1;
I2C_HandleTypeDef hi2c2;
I2C_HandleTypeDef hi2c3;

TIM_HandleTypeDef htim2;
TIM_HandleTypeDef htim3;
TIM_HandleTypeDef htim10;

UART_HandleTypeDef huart2;

/* USER CODE BEGIN PV */
Battery battery;
uint32_t values_adc[4];

TOF_VL53L0X TOF1;
TOF_VL53L0X TOF2;
TOF_VL53L0X TOF3;
TOF_VL53L0X TOF4;
TOF_VL53L0X TOF5;
TOF_VL53L0X TOF6;

uint32_t refSpadCount;
uint8_t isApertureSpads;
uint8_t VhvSettings;
uint8_t PhaseCal;
/* USER CODE END PV */

void SystemClock_Config(void);
static void MX_GPIO_Init(void);
static void MX_DMA_Init(void);
static void MX_I2C1_Init(void);
static void MX_I2C3_Init(void);
static void MX_ADC1_Init(void);
static void MX_I2C2_Init(void);
static void MX_USART2_UART_Init(void);
static void MX_TIM2_Init(void);
static void MX_TIM3_Init(void);
static void MX_TIM10_Init(void);
/**
  * @brief  The application entry point.
  * @retval int
  */
int main(void)
{
  /* MCU Configuration--------------------------------------------------------*/

  /* Reset of all peripherals, Initializes the Flash interface and the Systick. */
  HAL_Init();

  /* Configure the system clock */
  SystemClock_Config();

  /* Initialize all configured peripherals */
  MX_GPIO_Init();
  MX_DMA_Init();
  MX_I2C1_Init();
  MX_I2C3_Init();
  MX_ADC1_Init();
  MX_I2C2_Init();
  MX_USART2_UART_Init();
  MX_TIM2_Init();
  MX_TIM3_Init();
  MX_TIM10_Init();
  /* USER CODE BEGIN 2 */
  HAL_TIM_PWM_Start(&htim2, TIM_CHANNEL_1);
  HAL_TIM_PWM_Start(&htim3, TIM_CHANNEL_1);
  HAL_TIM_PWM_Start(&htim3, TIM_CHANNEL_2);
  HAL_ADC_Start_DMA(&hadc1, values_adc, 4);

  TOF_VL53L0X_init_all();
  HAL_TIM_Base_Start_IT(&htim10);

  display_init();
  display_printf(15, 20, DISPLAY_COLOR_WHITE, display_font_7x10, "Miras minisumo");
  display_render();
  battery.adc_reading = values_adc[0];
  initAverage(& (battery.adc_average), battery.adc_reading);
  //HAL_Delay(500);
  /* USER CODE END 2 */

  /* Infinite loop */
  /* USER CODE BEGIN WHILE */
  while (1)
  {
	if(HAL_GPIO_ReadPin(SW1_GPIO_Port, SW1_Pin) == 1)
		wait_for_fight_start();
	else
		debug_screen();
    /* USER CODE END WHILE */

    /* USER CODE BEGIN 3 */
  }
  /* USER CODE END 3 */
}

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
/* USER CODE BEGIN 4 */
void HAL_TIM_PeriodElapsedCallback(TIM_HandleTypeDef *htim){
	if(htim->Instance == TIM10){
		VL53L0X_GetRangingMeasurementData(&TOF2.vl53l0x_c, &TOF2.RangingData);
		VL53L0X_ClearInterruptMask(&TOF2.vl53l0x_c, VL53L0X_REG_SYSTEM_INTERRUPT_GPIO_NEW_SAMPLE_READY);

		VL53L0X_GetRangingMeasurementData(&TOF3.vl53l0x_c, &TOF3.RangingData);
		VL53L0X_ClearInterruptMask(&TOF3.vl53l0x_c, VL53L0X_REG_SYSTEM_INTERRUPT_GPIO_NEW_SAMPLE_READY);

		VL53L0X_GetRangingMeasurementData(&TOF4.vl53l0x_c, &TOF4.RangingData);
		VL53L0X_ClearInterruptMask(&TOF4.vl53l0x_c, VL53L0X_REG_SYSTEM_INTERRUPT_GPIO_NEW_SAMPLE_READY);

		VL53L0X_GetRangingMeasurementData(&TOF5.vl53l0x_c, &TOF5.RangingData);
		VL53L0X_ClearInterruptMask(&TOF5.vl53l0x_c, VL53L0X_REG_SYSTEM_INTERRUPT_GPIO_NEW_SAMPLE_READY);

	}
}
/* USER CODE END 4 */
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


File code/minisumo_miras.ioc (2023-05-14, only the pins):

Mcu.UserName=STM32F411RETx
PA12.GPIO_Label=TOF_X4
PA12.Signal=GPIO_Output
PA13.Signal=SYS_JTMS-SWDIO
PA14.Signal=SYS_JTCK-SWCLK
PA15.GPIO_Label=servo
PA15.Signal=S_TIM2_CH1_ETR
PA2.Signal=USART2_TX
PA3.Signal=USART2_RX
PA4.GPIO_Label=SW4
PA4.Signal=GPIO_Input
PA5.GPIO_Label=SW3
PA5.Signal=GPIO_Input
PA6.GPIO_Label=motor_R_PWM
PA6.Signal=S_TIM3_CH1
PA7.GPIO_Label=SW2
PA7.Signal=GPIO_Input
PA8.Signal=I2C3_SCL
PB0.GPIO_Label=motor_R_DIR_2
PB0.Signal=GPIO_Output
PB1.GPIO_Label=adc_bat_meas
PB1.Signal=ADCx_IN9
PB10.Signal=I2C2_SCL
PB12.GPIO_Label=starter
PB12.Signal=GPIO_Input
PB13.GPIO_Label=user_LED
PB13.Signal=GPIO_Output
PB14.GPIO_Label=TOF_X5
PB14.Signal=GPIO_Output
PB2.GPIO_Label=motor_R_DIR_1
PB2.Signal=GPIO_Output
PB3.Signal=I2C2_SDA
PB5.GPIO_Label=motor_L_PWM
PB5.Signal=S_TIM3_CH2
PB6.Signal=I2C1_SCL
PB7.Signal=I2C1_SDA
PB8.GPIO_Label=motor_L_DIR_1
PB8.Signal=GPIO_Output
PB9.GPIO_Label=motor_L_DIR_2
PB9.Signal=GPIO_Output
PC1.GPIO_Label=adc_line_sensor1
PC1.Signal=ADCx_IN11
PC11.GPIO_Label=LS_ON
PC11.Signal=GPIO_Output
PC13-ANTI_TAMP.GPIO_Label=TOF_X3
PC13-ANTI_TAMP.Signal=GPIO_Output
PC14-OSC32_IN.GPIO_Label=TOF_X2
PC14-OSC32_IN.Signal=GPIO_Output
PC15-OSC32_OUT.GPIO_Label=TOF_X1
PC15-OSC32_OUT.Signal=GPIO_Output
PC2.GPIO_Label=adc_line_sensor2
PC2.Signal=ADCx_IN12
PC3.GPIO_Label=adc_line_sensor3
PC3.Signal=ADCx_IN13
PC4.GPIO_Label=SW1
PC4.Signal=GPIO_Input
PC5.GPIO_Label=TOF_X6
PC5.Signal=GPIO_Output
PC9.Signal=I2C3_SDA

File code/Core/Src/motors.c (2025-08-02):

/**
 * @file motors.c
 * @author Dominik
 * @brief
 * @version 0.1
 * @date 2023-05-6
 *
 * @copyright Copyright (c) 2023
 *
 */

#include "motors.h"

/**
 * @brief
 *
 * @param speed 0-100
 */
void motor_L_set_speed(uint8_t speed){
	if(speed < 0)
		speed = 0;
	else if(speed > 100)
		speed = 100;
	__HAL_TIM_SET_COMPARE(&htim3, TIM_CHANNEL_2, speed);
}

/**
 * @brief
 *
 * @param speed 0-100
 */
void motor_R_set_speed(uint8_t speed){
	if(speed < 0)
		speed = 0;
	else if(speed > 100)
		speed = 100;
	__HAL_TIM_SET_COMPARE(&htim3, TIM_CHANNEL_1, speed);
}

void motor_L_set_direction(motor_direction direction){
	switch(direction){
		case FORWARD:
			HAL_GPIO_WritePin(motor_L_DIR_1_GPIO_Port, motor_L_DIR_1_Pin, GPIO_PIN_RESET);
			HAL_GPIO_WritePin(motor_L_DIR_2_GPIO_Port, motor_L_DIR_2_Pin, GPIO_PIN_SET);
			break;
		case BACKWARD:
			HAL_GPIO_WritePin(motor_L_DIR_1_GPIO_Port, motor_L_DIR_1_Pin, GPIO_PIN_SET);
			HAL_GPIO_WritePin(motor_L_DIR_2_GPIO_Port, motor_L_DIR_2_Pin, GPIO_PIN_RESET);
			break;
	}
}

void motor_R_set_direction(motor_direction direction){
	switch(direction){
		case FORWARD:
			HAL_GPIO_WritePin(motor_R_DIR_1_GPIO_Port, motor_R_DIR_1_Pin, GPIO_PIN_SET);
			HAL_GPIO_WritePin(motor_R_DIR_2_GPIO_Port, motor_R_DIR_2_Pin, GPIO_PIN_RESET);
			break;
		case BACKWARD:
			HAL_GPIO_WritePin(motor_R_DIR_1_GPIO_Port, motor_R_DIR_1_Pin, GPIO_PIN_RESET);
			HAL_GPIO_WritePin(motor_R_DIR_2_GPIO_Port, motor_R_DIR_2_Pin, GPIO_PIN_SET);
			break;
	}
}

/**
 * @brief
 *
 * @param eangle 0-180
 */
void servo_set_eangle(uint8_t eangle){
	uint16_t pulse_duration;

	pulse_duration = MIN_PULSE_SERVO + ((eangle * STEP) / 1000);

	__HAL_TIM_SET_COMPARE(&htim2, TIM_CHANNEL_1, pulse_duration);
}

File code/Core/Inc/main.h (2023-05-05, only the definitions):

#define TOF_X3_Pin GPIO_PIN_13
#define TOF_X3_GPIO_Port GPIOC
#define TOF_X2_Pin GPIO_PIN_14
#define TOF_X2_GPIO_Port GPIOC
#define TOF_X1_Pin GPIO_PIN_15
#define TOF_X1_GPIO_Port GPIOC
#define XTAL_Pin GPIO_PIN_0
#define XTAL_GPIO_Port GPIOH
#define XTALH1_Pin GPIO_PIN_1
#define XTALH1_GPIO_Port GPIOH
#define adc_line_sensor1_Pin GPIO_PIN_1
#define adc_line_sensor1_GPIO_Port GPIOC
#define adc_line_sensor2_Pin GPIO_PIN_2
#define adc_line_sensor2_GPIO_Port GPIOC
#define adc_line_sensor3_Pin GPIO_PIN_3
#define adc_line_sensor3_GPIO_Port GPIOC
#define SW4_Pin GPIO_PIN_4
#define SW4_GPIO_Port GPIOA
#define SW3_Pin GPIO_PIN_5
#define SW3_GPIO_Port GPIOA
#define motor_R_PWM_Pin GPIO_PIN_6
#define motor_R_PWM_GPIO_Port GPIOA
#define SW2_Pin GPIO_PIN_7
#define SW2_GPIO_Port GPIOA
#define SW1_Pin GPIO_PIN_4
#define SW1_GPIO_Port GPIOC
#define TOF_X6_Pin GPIO_PIN_5
#define TOF_X6_GPIO_Port GPIOC
#define motor_R_DIR_2_Pin GPIO_PIN_0
#define motor_R_DIR_2_GPIO_Port GPIOB
#define adc_bat_meas_Pin GPIO_PIN_1
#define adc_bat_meas_GPIO_Port GPIOB
#define motor_R_DIR_1_Pin GPIO_PIN_2
#define motor_R_DIR_1_GPIO_Port GPIOB
#define starter_Pin GPIO_PIN_12
#define starter_GPIO_Port GPIOB
#define user_LED_Pin GPIO_PIN_13
#define user_LED_GPIO_Port GPIOB
#define TOF_X5_Pin GPIO_PIN_14
#define TOF_X5_GPIO_Port GPIOB
#define TOF_X4_Pin GPIO_PIN_12
#define TOF_X4_GPIO_Port GPIOA
#define servo_Pin GPIO_PIN_15
#define servo_GPIO_Port GPIOA
#define LS_ON_Pin GPIO_PIN_11
#define LS_ON_GPIO_Port GPIOC
#define motor_L_PWM_Pin GPIO_PIN_5
#define motor_L_PWM_GPIO_Port GPIOB
#define motor_L_DIR_1_Pin GPIO_PIN_8
#define motor_L_DIR_1_GPIO_Port GPIOB
#define motor_L_DIR_2_Pin GPIO_PIN_9
#define motor_L_DIR_2_GPIO_Port GPIOB

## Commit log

2022-11-15 added stm32f411
    [mcu_board.brd, mcu_board.sch]
2022-11-29 renamed files, added H bridge
    [main_board.brd, main_board.sch, mcu_board.brd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]
2022-12-01 finished v1
    [line_sensor.brd, line_sensor.sch]
2022-12-28 sensors on main pcb
    [line_sensor.brd, line_sensor.sch, main_board.brd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]
2022-12-28 line sensor
2022-12-29 pcb shape
    [main_board.brd, main_board.sch]
2023-01-16 power routed more or less
    [main_board.brd, main_board.sch]
2023-02-24 branch fix xd
    [Assembly3.0003.iam, Assembly3.iam, MicroGearmotor v3.ipt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]
2023-03-11 almost there
    [main_board.brd, main_board.sch]
2023-03-11 before 2 H-bridges
    [main_board.brd, main_board.sch]
2023-03-12 2 h-bridges, 5V reg
    [main_board.brd, main_board.sch]
2023-03-12 almost done
    [main_board.brd, main_board.sch]
2023-03-13 main pcb done
    [main_board.brd, main_board.sch]
2023-03-19 improved routing
    [main_board.brd]
2023-03-19 corrected on
    [main_board.brd, main_board.sch]
2023-03-26 finished v1.0
    [pcb_top.brd, pcb_top.sch]
2023-03-26 minor changes
    [pcb_top.brd, pcb_top.sch]
2023-04-29 oled and battery meas. works
2023-04-30 adc KTIR works
2023-05-01 TOF distance sensor works
2023-05-05 servo works kinda
2023-05-05 battery defines
2023-05-06 servo and motors work
2023-05-10 fixed clock, before more TOFs
    [main.c, minisumo_miras.ioc, modes_of_operation.c]
2024-03-15 adjust component values
    [main_board.brd, main_board.sch, pcb_top.brd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]
2025-03-12 proba zmiany silnikow
    [Miras.0014.iam, Miras.0015.iam, Miras.iam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]
2025-03-16 zmiany silnika 1
    [Miras.0015.iam, Miras.0017.iam, Miras.iam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]
2025-03-19 zmiany uchwytu gornego
    [Miras.0017.iam, Miras.0019.iam, Miras.iam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]
2025-04-09 added pololu motors mount
    [Miras.0023.iam, Miras.0025.iam, Miras.iam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]
2025-08-02 Fix code folder structure, delete Debug folder
    [battery.c, display.c, main.c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]

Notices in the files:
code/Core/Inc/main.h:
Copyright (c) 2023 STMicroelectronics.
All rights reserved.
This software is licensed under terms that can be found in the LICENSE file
